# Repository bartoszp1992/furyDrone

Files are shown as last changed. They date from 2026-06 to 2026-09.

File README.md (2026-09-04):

# BD1 "Fury" repo

**Fury is 3" sub250 freestyle type drone, for 3S/4S batteries, with fully 3D printed construction**

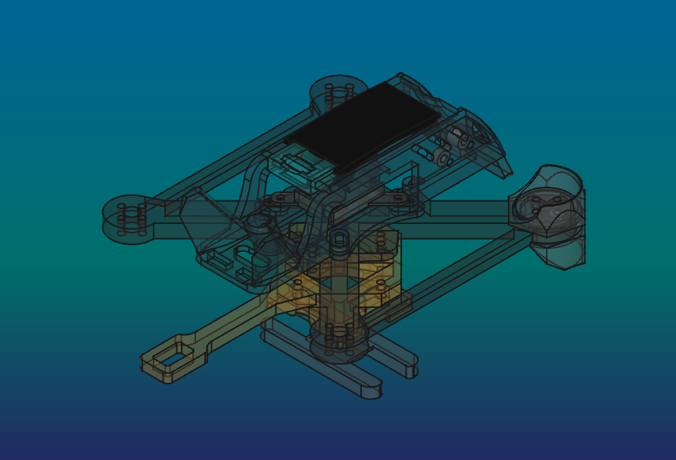
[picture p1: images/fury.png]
Fury
 

*Speed can be reduced in edgeTX system using logical switch based on the speed read from GNSS, and the mix function. The project includes a configuration that can limit speed*

## 3D printing

All on 0.4 brass nozzle, make sure you have at least 5 pieces- CF filaments will wear off quickly. Trim Z-offset after every CF print

I don't recommend using SS nozzle becouse it's too cold for my printer.

### tips/info
>please use proper materials. Drone components will be hot or very hot. Printing parts with PLA or similar will cause melt your construction during flight. **If my cheap Sidewinder X4 printer can handle this materials- yours printer also can.**

>It's not cheap project- don't do it because of lack of funds. Buying a ready frame will be cheaper than buying CF filaments

>one battery for one 2-3 minutes flight. Make sure you have more than 1

### parts
- **body**
: PA12
- **bottom**
: PA12
- **bumper**
: PP/TPU A95
- **Sleeves**
: PETG
- **foot**
: PA12
- **frame**
: PC-CF/PETG-CF/PAHT-CF, 3 wall loops, no supports, 100% grid infill, rotate 15deg in Z axis
- **light plate**
: TPU A95
- **motor screw shim**
: PC
- **roof**
: TPU A95 / PP
- **top lock**
: PETG
- **VTX adapter**
: TPU A95

## BOM

### 3D printed
- 1 x body
- 1 x bottom
- 4 x bumpers(optional)
- 2 x camera sleeves
- 4 x sleeve 2mm
- 4 x sleeve 3mm
- 16 x 1.2mm sleeve for frame30 (optional)
- 1 x foot(optional)
- 1 x frame
- 1 x light plate
- 1 x motor screw shim
- 1 x roof
- 1 x top lock
- 1x VTX adapter (optional)

### electronic
- [ ] **FC**
: GEPRC TAKER G4 35A AIO
>you can use any other 35A+, compatible with 3/4S and 25,5mm pitch
- [ ] **propellers 3"**
: HQPROP T3X1.8X3 / HQPROP T3X3
- [ ] **motors 3"**
: flyfishRC FLASH 1404 4500KV
- [ ] **receiver**
: SpeedyBee Nano 2.4G ExpressLRS ELRS Receiver
>or any other ELRS receiver which can fit into modules mounts in body
- [ ] **camera analog**
: CADDX Ratel Pro
- [ ] **VTX analog**
: TBS Unify Pro32 Nano 5G8
- [ ] **Camera + VTX digital**
: BETAFPV P1 Air unit
- [ ] **battery 3"**
: LAVA II 4S 680mAh 95C
- [ ] **GNSS**
: Foxeer M10Q-180 compass- mount on **right** fame spoke, faced antenna up and socket left(to body)
- [ ] **Controller**
: RM Pocket, or any other with ELRS and edgeTX
- [ ] **Goggles**
: EMAX Transporter II
- [ ] **VRX antenna**
: Any
- [ ] **Charger**
: iMax B6 V2 with some 12V supplier / ToolkitRC Q4AC
- [ ] **4x RGB LED**
: if you want make night flies
- [ ] **2 x additional XT30 connectors set**
: to connect battery to charger and FC
- [ ] **red and black 18AWG silicon wire cables**
: to make connection with FC
- [ ] **14x9x5 (diameter * hole * height) ferrite ring**
: turn 3-4x GNSS cable as close as possible to GNSS modulestabilizer

### mechanical

- [ ] 1x 10x130-150mm battery velcro strap
- [ ] 8x 20mm M2 screws with barrel head for stack mount
- [ ] 4x 10mm M2 screws with barrel head for body mount
- [ ] 8x M2 H3 D3.6mm brass insert
- [ ] 2-4x M2 1,6mm nut to lock stack screws
- [ ] 4x M2 20mm PA screws to mount digital VTX
- [ ] 4x M2 0,8mm nut to screw in digital VTX
- [ ] 16x M2 8mm screws for frame30
- [ ] 16x M2 10mm screws for frame30 with motor screw shims

## electronics
project contains configuration for HD version with BZ- pin used as VTX power switch. Implementation below:
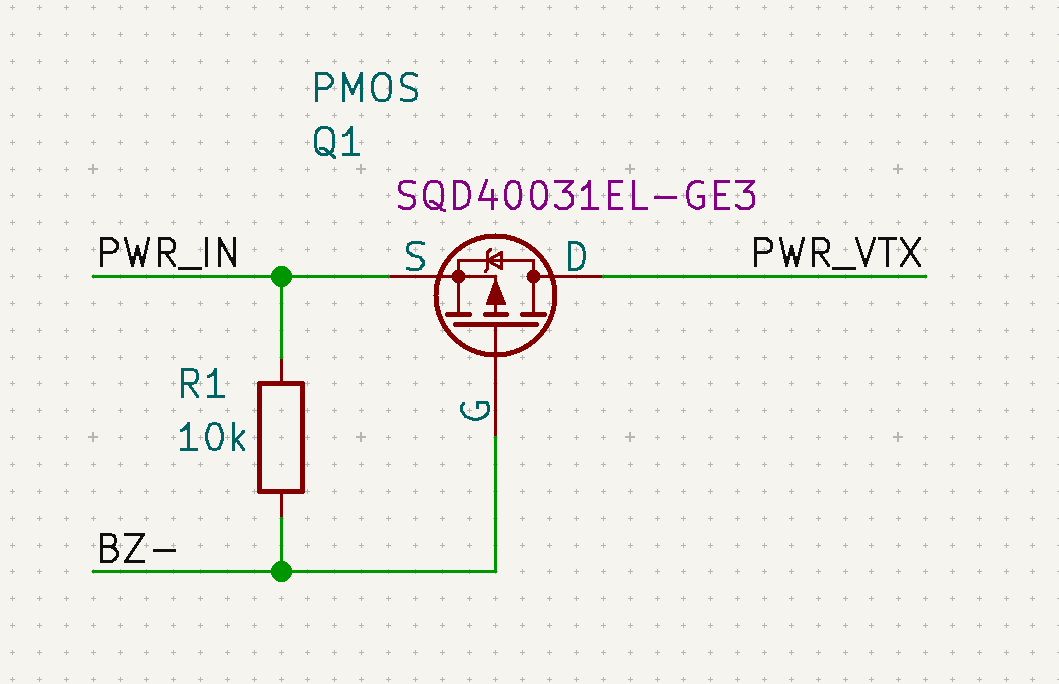
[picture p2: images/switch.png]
VTX power switch


**Thanks Baro for PID tunes!!**
*BD1 stands for "Bart's Design 1"*

# firmware
If you are building remotely:
> choose analog OSD Protocol and type **OSD_HD** in custom defines, to build firmware with both- digital and analog OSD 
> In other options add **Magnetometers**, **Position Hold** and **Altitude Hold**

## notice
This repository includes third-party firmware binaries used by this FPV drone.

### Betaflight

Versions:
- `2025.12.2`

Included firmware:

- `betaflight_2025.12.2_STM32G47X_TAKERG4AIO_839441c9.hex`

These firmware files were generated using the official Betaflight Cloud
Build service.

Flight controller targets:

- `TAKERG4AIO`

Additional build options used for this project:

- Analog OSD
- `OSD_HD`
- Magnetometers (`MAG`)
- Position Hold (`POSITION_HOLD`)
- Altitude Hold (`ALTITUDE_HOLD`)

No modifications were made to the Betaflight source code by this repository.
The options listed above are compile-time options supported by the official
Betaflight build system.

Corresponding source:

https://github.com/betaflight/betaflight
Tag corresponding to firmware version.

Betaflight is distributed under the GNU General Public License version 3.
A copy of the GNU GPL v3 is included in this repository as `GPL-3.0.txt`.

### Bluejay

Version: `v0.21.0`

Included firmware:

- `J_H_15_48_v0.21.0.hex`

This is an unmodified Bluejay firmware binary from the upstream
`v0.21.0` release.

Corresponding source:

Bluejay repository, tag `v0.21.0`.

Bluejay is distributed under the GNU General Public License version 3.
A copy of the GNU GPL v3 is included in this repository as `LICENSE.txt`.

### Copyright and attribution

Betaflight and Bluejay are independent open-source projects.
Copyright remains with their respective authors and contributors.

This repository does not claim ownership of Betaflight or Bluejay and is
not affiliated with or endorsed by either project.

[Betaflight](https://github.com/betaflight/betaflight/tree/2025.12.2)

[Bluejay](https://github.com/bird-sanctuary/bluejay/tree/v0.21.0)

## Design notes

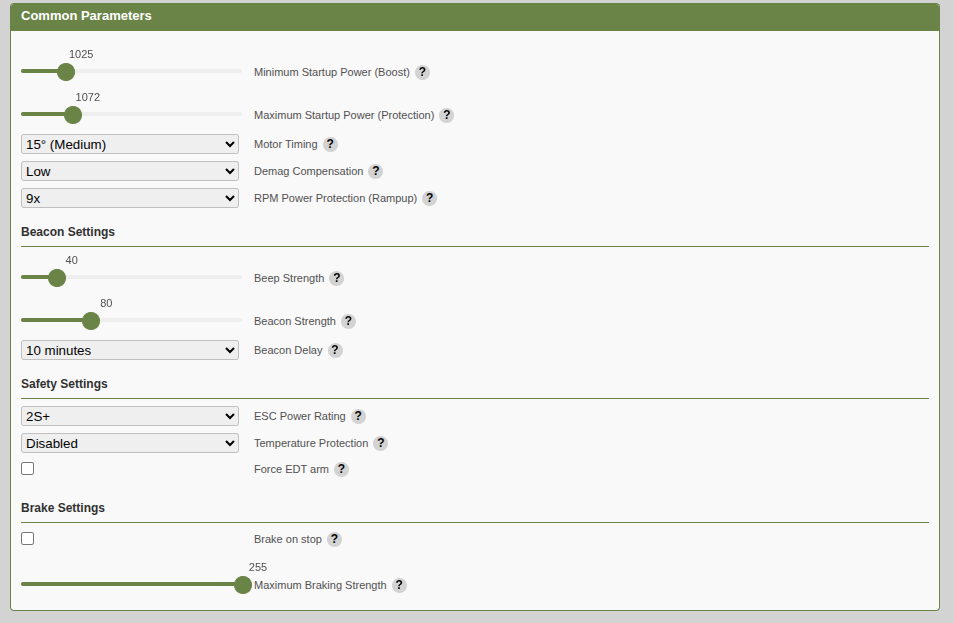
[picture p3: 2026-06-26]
FC/GEPRC TAKER G4 35A AIO/ESC config/config 7200KV.png

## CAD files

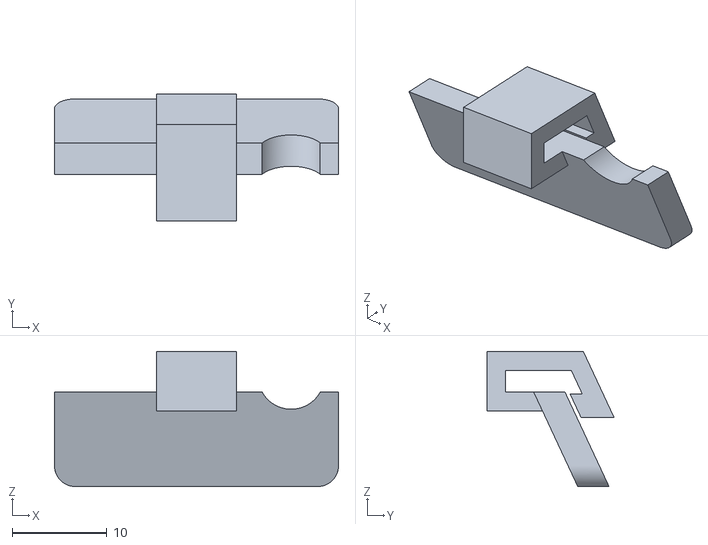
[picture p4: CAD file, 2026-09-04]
mechanical/output/parts_drone-light plate.stl
30.0 x 13.5 x 14.3

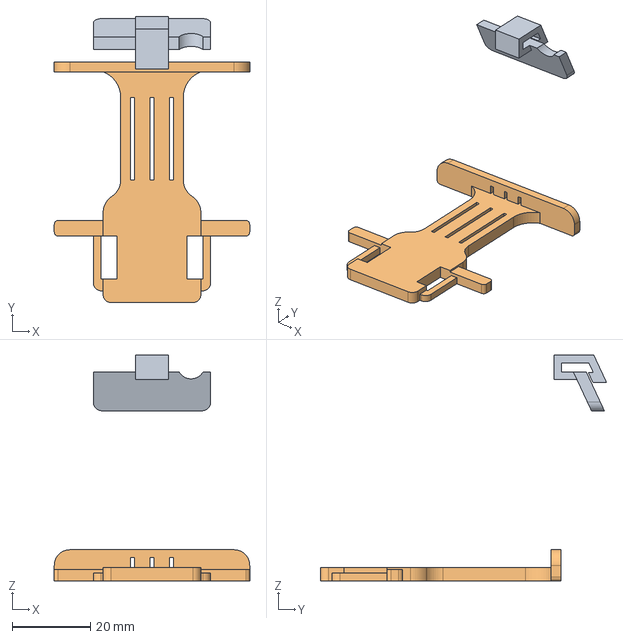
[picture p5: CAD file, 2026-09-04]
mechanical/parts/parts_drone.FCStd
50.0 x 73.2 x 57.8 mm
light plate
foot30-LC

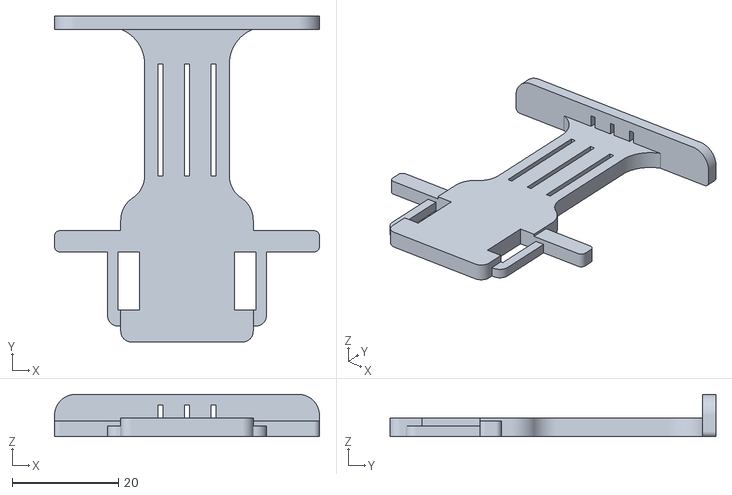
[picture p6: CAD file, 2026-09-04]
mechanical/output/parts_drone-foot30-LC.stl
50.0 x 61.5 x 8.00

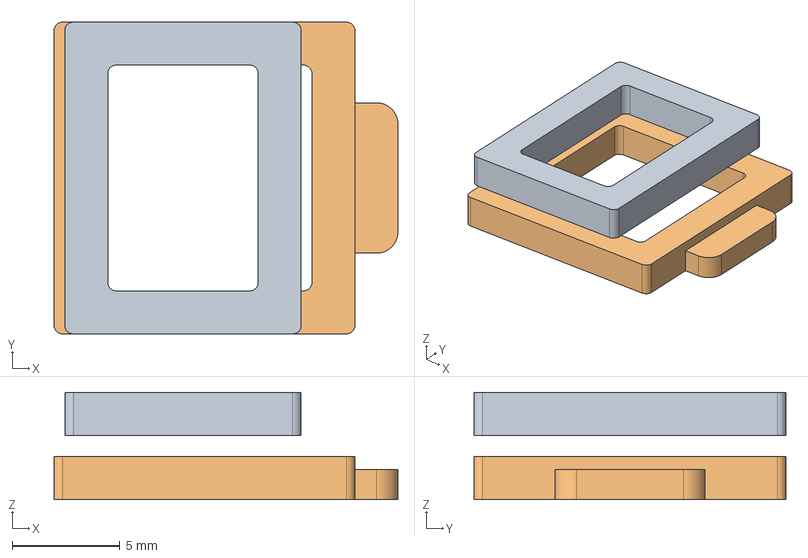
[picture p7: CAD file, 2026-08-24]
mechanical/parts/parts_strapDD.FCStd
16.0 x 14.5 x 5.00 mm
external
internal

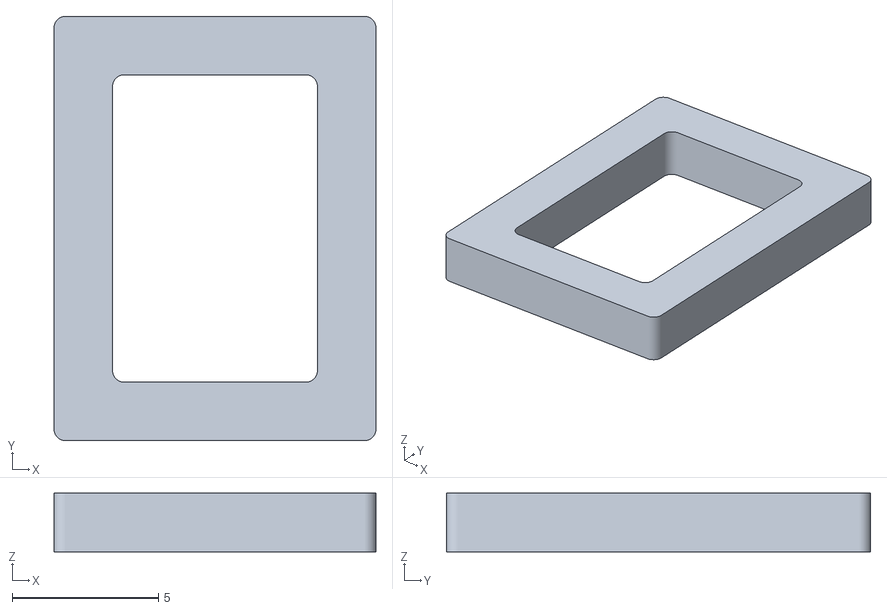
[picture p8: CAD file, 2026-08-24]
mechanical/output/parts_strapDD-external.stl
11.0 x 14.5 x 2.00

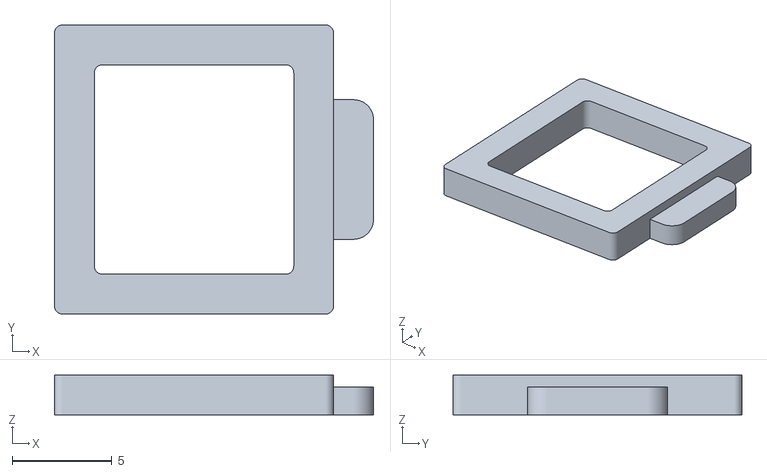
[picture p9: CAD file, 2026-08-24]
mechanical/output/parts_strapDD-internal.stl
16.0 x 14.5 x 2.00

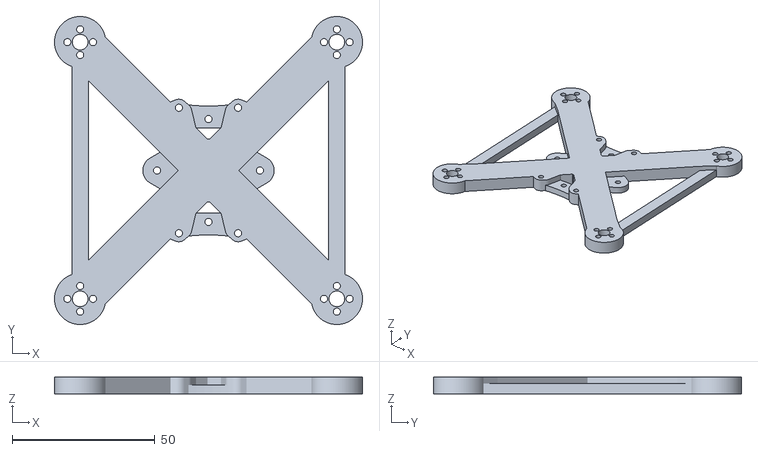
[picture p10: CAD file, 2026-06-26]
mechanical/output/parts_drone-frame30-R.stl
108.0 x 108.0 x 5.80

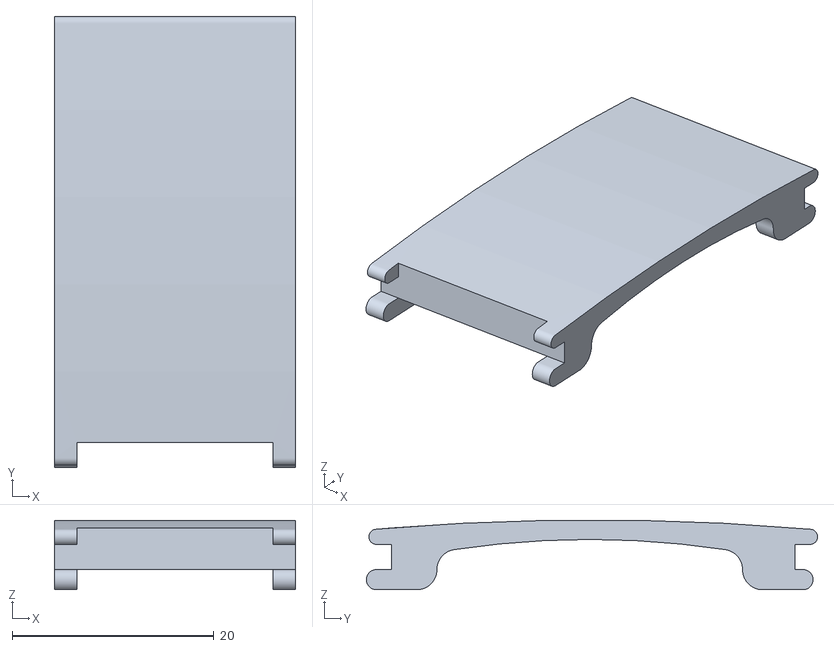
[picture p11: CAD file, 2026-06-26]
mechanical/output/parts_drone-roof.stl
23.9 x 44.7 x 6.89

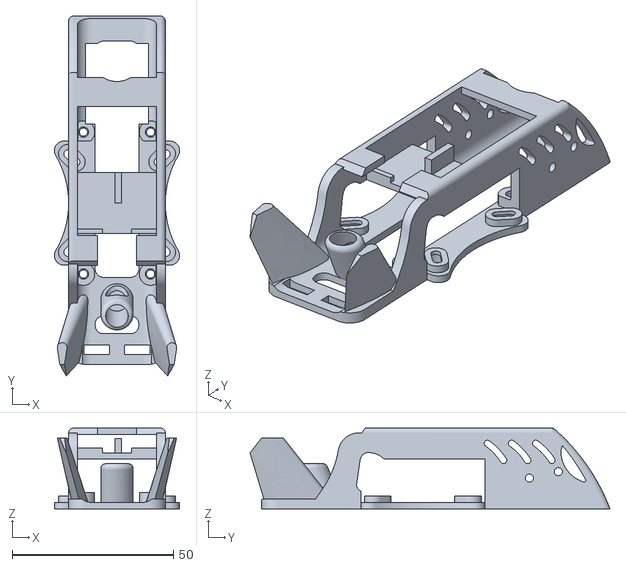
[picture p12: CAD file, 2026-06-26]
mechanical/output/parts_drone-body-SD_HD.stl
38.8 x 111.6 x 25.0

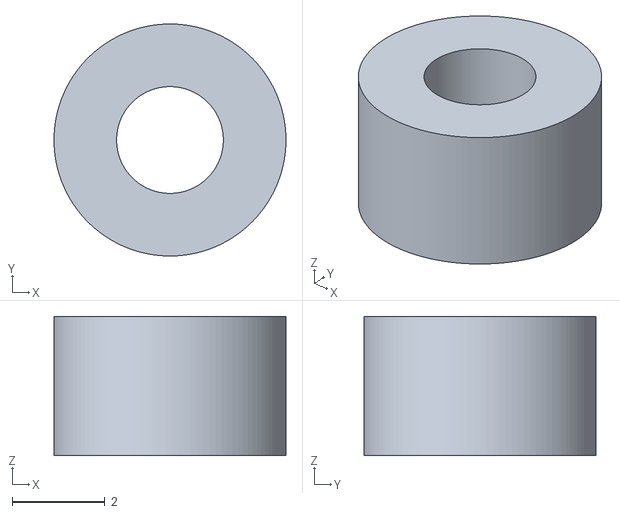
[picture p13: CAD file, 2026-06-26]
mechanical/output/parts_drone-sleeve 3mm.stl
5.00 x 5.00 x 3.00

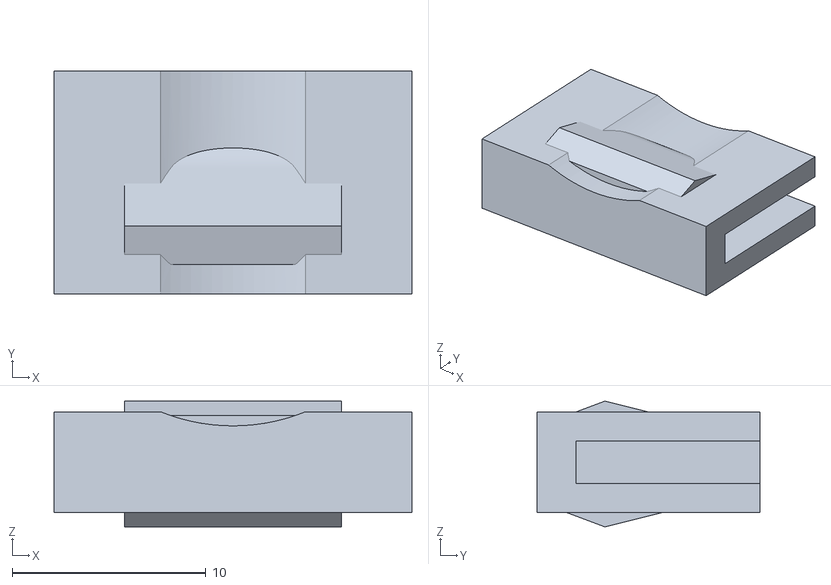
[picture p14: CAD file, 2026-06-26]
mechanical/output/parts_drone-top lock.stl
18.5 x 11.5 x 6.50

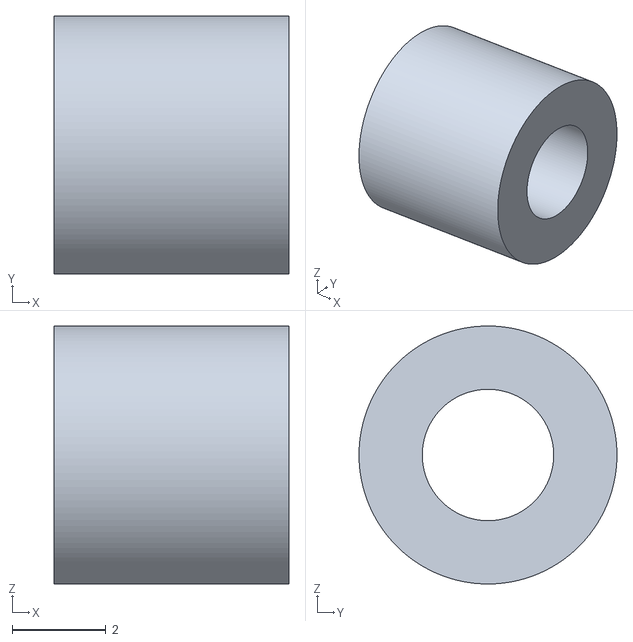
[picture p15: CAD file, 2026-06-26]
mechanical/output/parts_drone-cam trim sleeve1414.stl
5.00 x 5.50 x 5.50

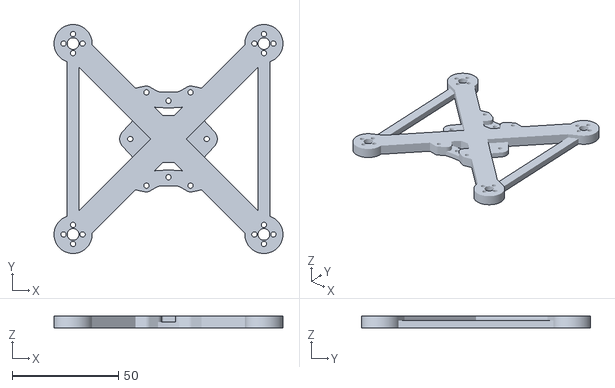
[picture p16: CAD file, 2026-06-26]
mechanical/output/parts_drone-frame30.stl
108.0 x 108.0 x 5.80

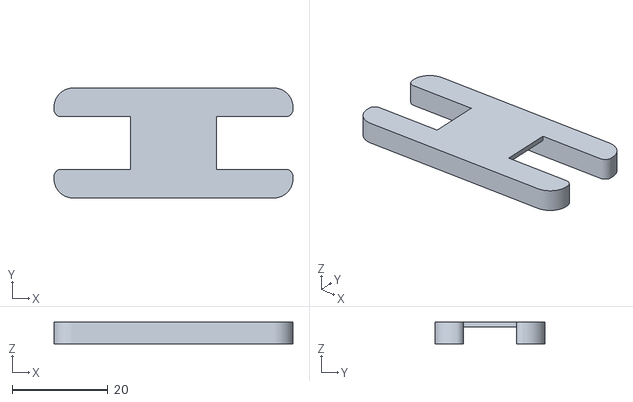
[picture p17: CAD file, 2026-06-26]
mechanical/output/parts_drone-foot30.stl
50.0 x 23.0 x 4.50

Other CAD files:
mechanical/output/parts_drone-bottom30.stl
mechanical/output/parts_drone-sleeve 2mm.stl
mechanical/output/parts_drone-cam trim sleeve1919.stl
mechanical/output/parts_drone-bumper30.stl
mechanical/output/parts_drone-VTX adapter.stl
mechanical/output/parts_drone-motor screw shim.stl
mechanical/output/parts_drone-sleeve 1.2mm.stl

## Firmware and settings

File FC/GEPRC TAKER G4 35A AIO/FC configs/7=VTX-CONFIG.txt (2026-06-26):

set vtx_band = 5
set vtx_channel = 4
set vtx_power = 1
set vtx_freq = 5769

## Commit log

2026-06-26 initial for fury
    [8=VTX-CONFIG.txt, parts_drone-VTX adapter.stl, parts_drone-body-SD_HD.stl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]
2026-06-27 props out
